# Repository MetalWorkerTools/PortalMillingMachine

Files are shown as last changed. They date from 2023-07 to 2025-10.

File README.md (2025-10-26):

# Portal Milling Machine
An easy to build portal milling machine for milling steel designed in FreeCad.
Most parts can be 3D printed to build the machine and milled out of aluminum when the machine is done to increase regidity.

Current progress: The machine is done except for a MQL system and some led illumination. I use the router for milling aluminum and steel and making PCB's. The result is pretty good but my manual mill is more rigid.
It would take about 100 hours to redo this machine from scratch. If you have a milling machine, you could directly make the aluminum version.

Backlash on all axis is somewhere between 0.01 and 0.03 mm.
I can adjust all axis to 0.02 mm / 100 mm.
The repeatability on all axis is better than 0.01 mm. (That is not the same as accuracy).
Without measuring, steel parts are within 0.1 mm. I haven't completed all tests but I expect that I can mill steel parts within 0.03 mm.
The self made 3000 RPM ER16 spindle is realy quit when milling. Because the frame is made from aluminium extrusion, the CNC router makes more noise than the manual mill under the same conditions.
The weight is about 55 kg.

For the next project I am going to CNC a manual mill that all ready has ball screws on the X and Y axis for more rigidity and lesser noise.

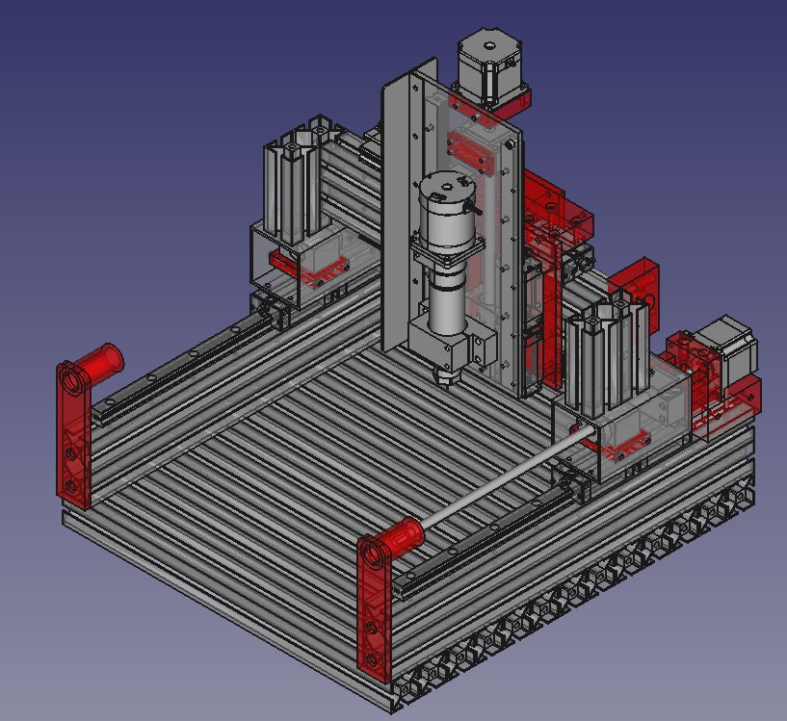
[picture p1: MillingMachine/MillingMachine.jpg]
MillingMachine


This page is under construction

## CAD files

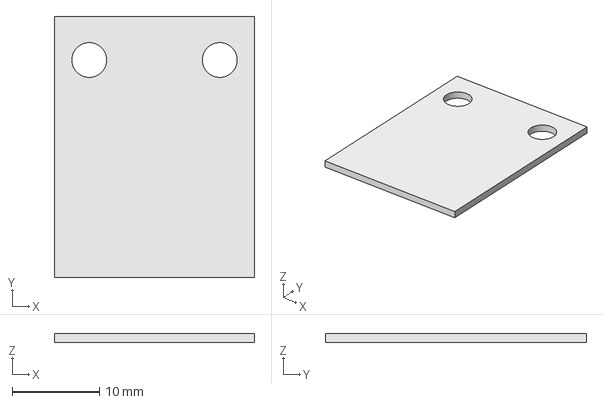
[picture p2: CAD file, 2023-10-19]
AirSuply/ValveMounting.FCStd
23.0 x 30.0 x 1.00 mm

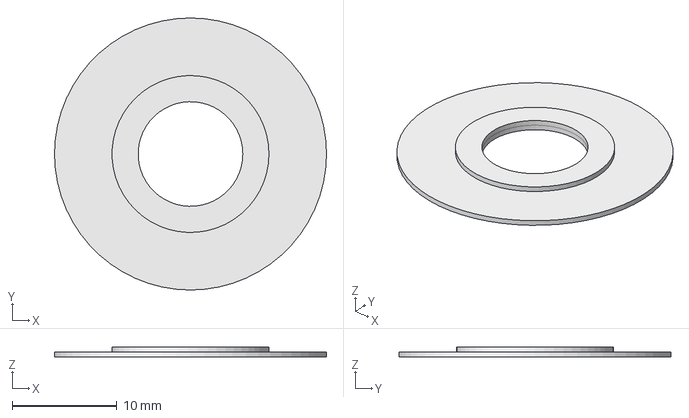
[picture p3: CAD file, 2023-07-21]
BK10BearingSpacer/BK10BearingSpacer.FCStd
26.0 x 26.0 x 1.00 mm

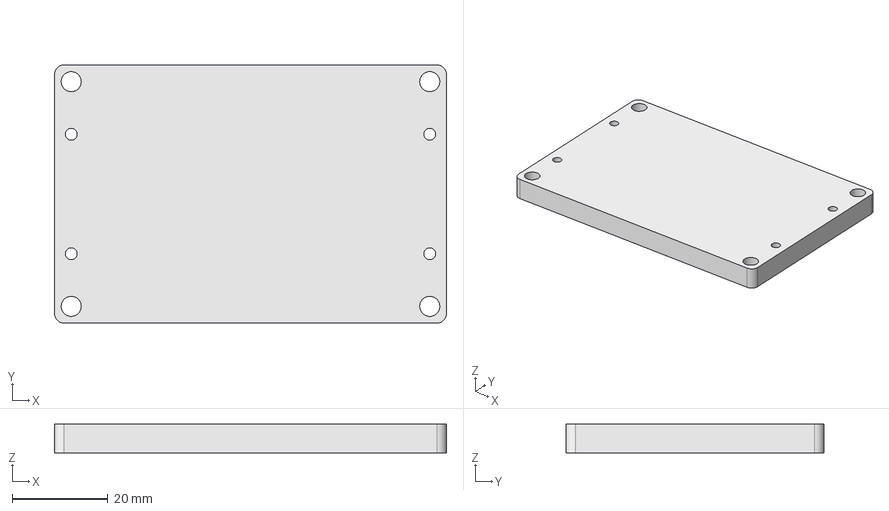
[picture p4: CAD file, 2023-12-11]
BLDC controller/BLDC controller.FCStd
82.0 x 54.0 x 6.00 mm

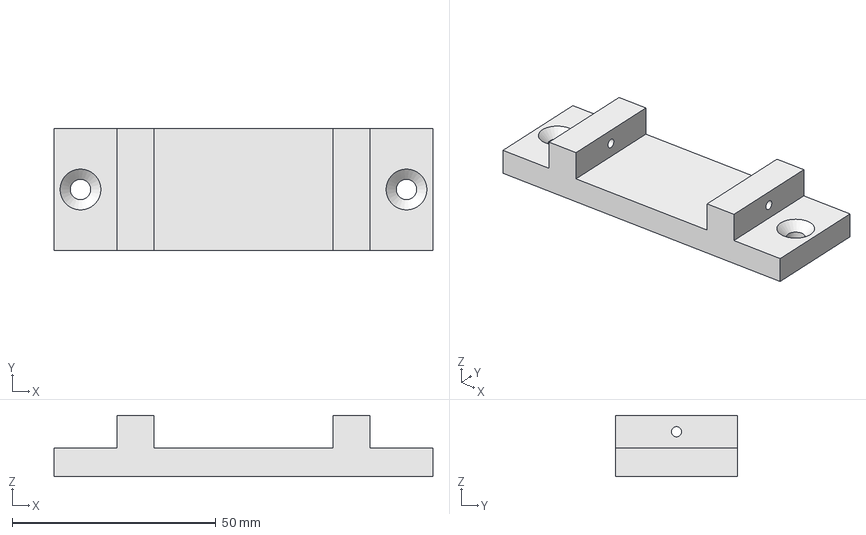
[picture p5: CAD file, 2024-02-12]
BridgeAngleAdjuster/BridgeAngleAdjuster.FCStd
93.0 x 30.0 x 15.0 mm

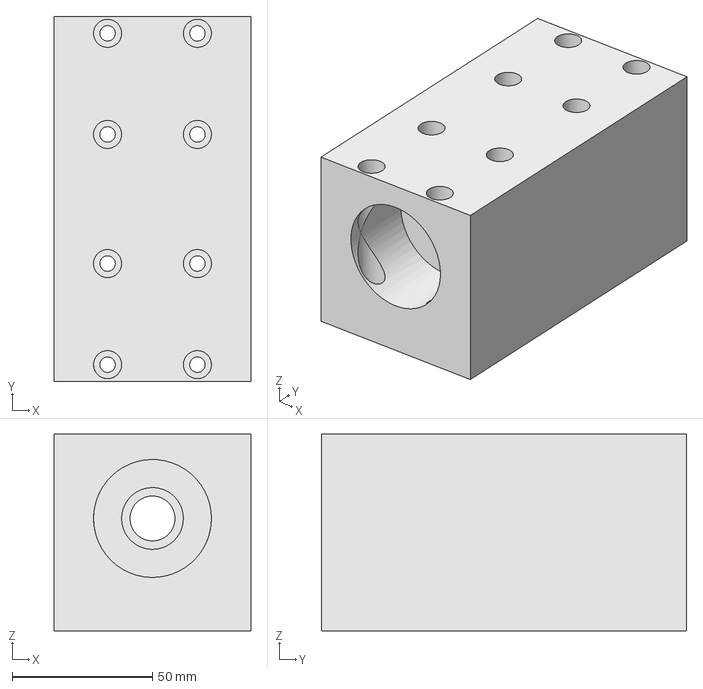
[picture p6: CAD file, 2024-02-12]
BridgeProfileSolid/BridgeProfileSolid.FCStd
70.0 x 130.0 x 70.0 mm

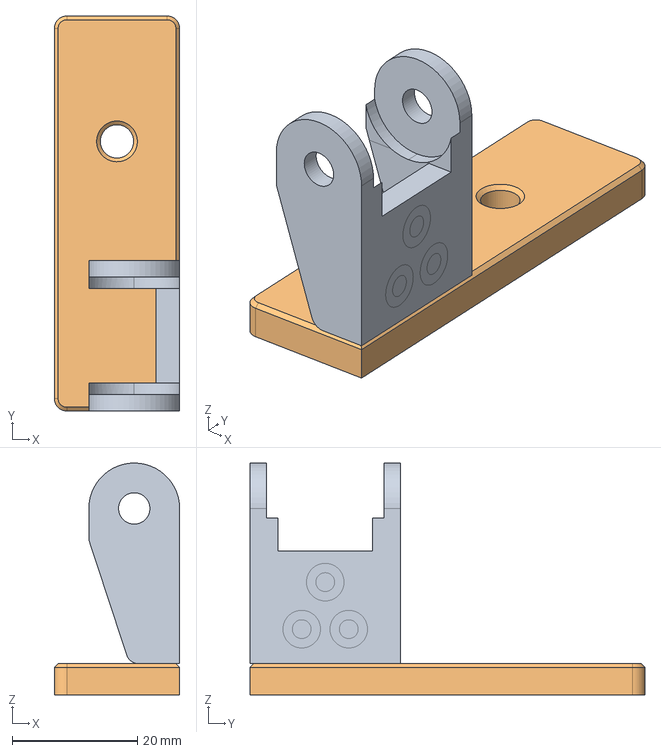
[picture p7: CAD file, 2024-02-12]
CableChain/CableChainMountXaxis.FCStd
20.0 x 63.0 x 37.0 mm
Chain
Base

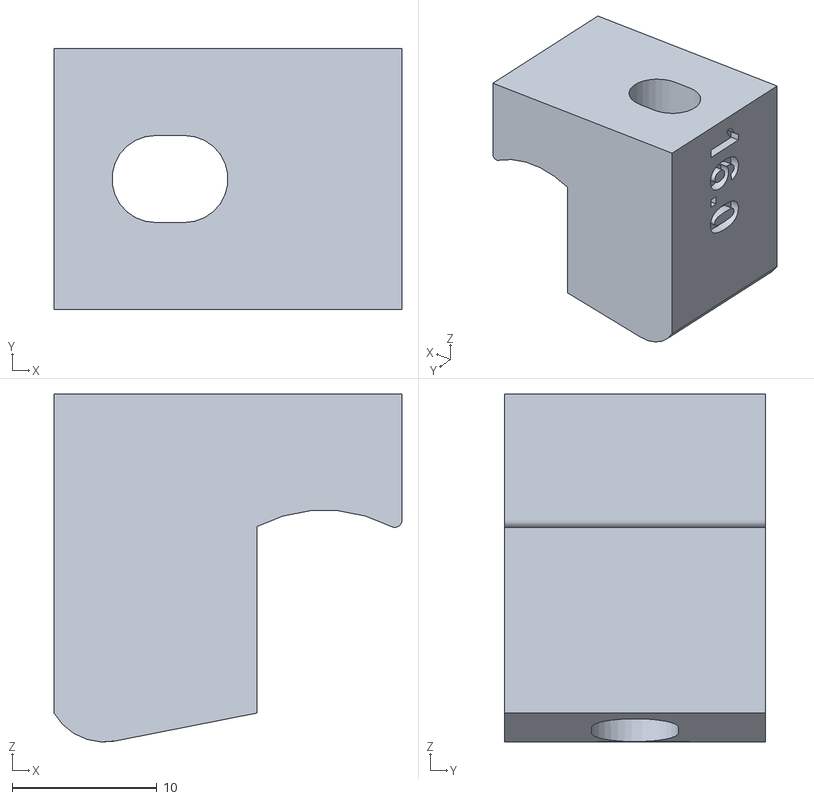
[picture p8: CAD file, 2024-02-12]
Clamps/ViceClamp.stl
24.0 x 18.0 x 24.0

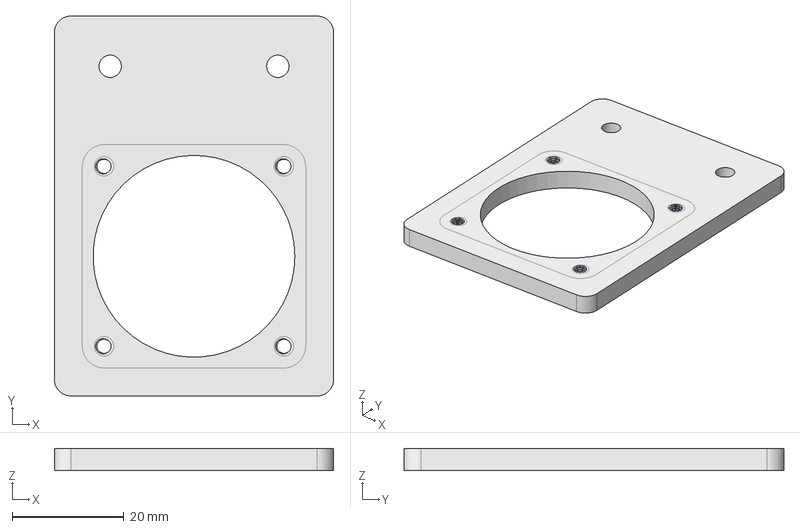
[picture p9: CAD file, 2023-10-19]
ControllerFanHolder/ControllerFanHolder.FCStd
50.0 x 68.0 x 4.00 mm

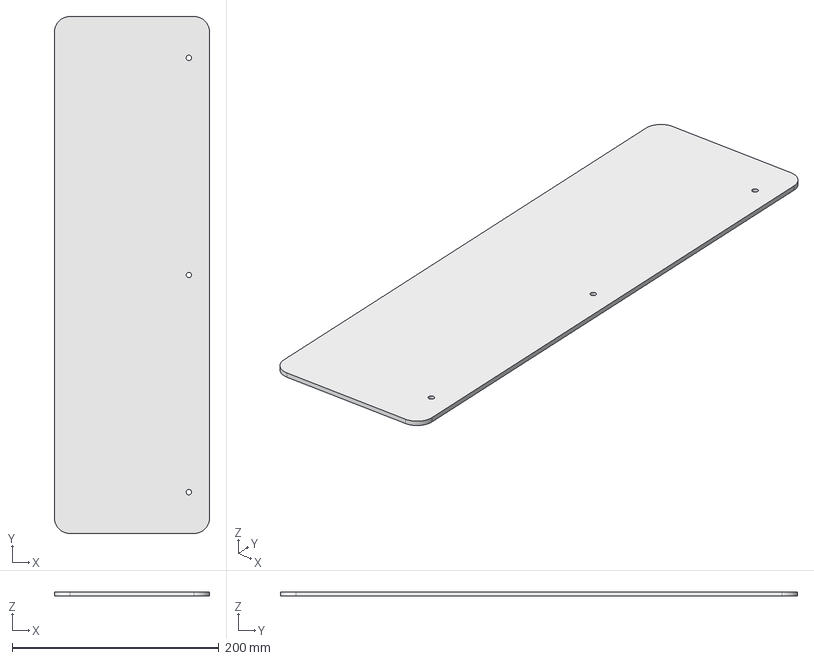
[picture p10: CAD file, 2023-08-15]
Covers/Covers.FCStd
150.0 x 500.0 x 4.00 mm

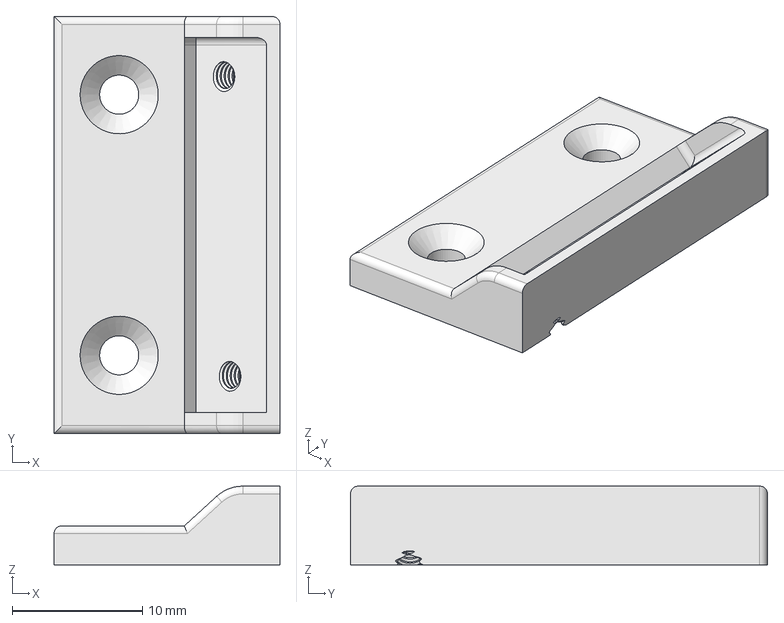
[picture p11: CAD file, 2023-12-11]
Display/DisplayHolder.FCStd
17.3 x 32.0 x 6.05 mm

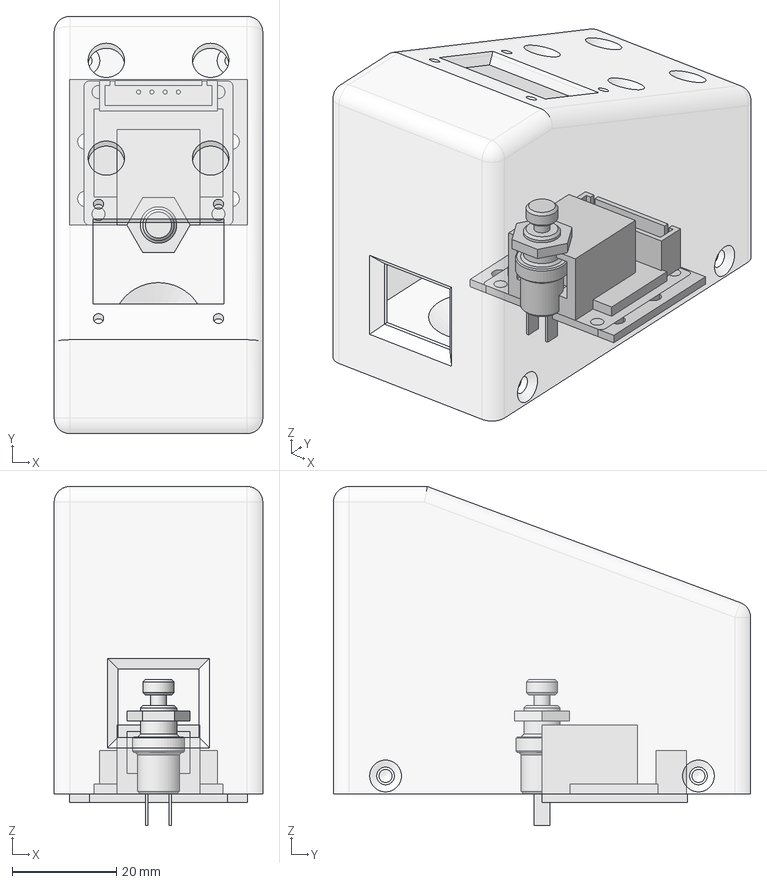
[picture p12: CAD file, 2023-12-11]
DisplayCase/DisplayCase.FCStd
40.0 x 80.0 x 65.0 mm
CaseBody
RJ45-JST-XH
Schakelaar
Display

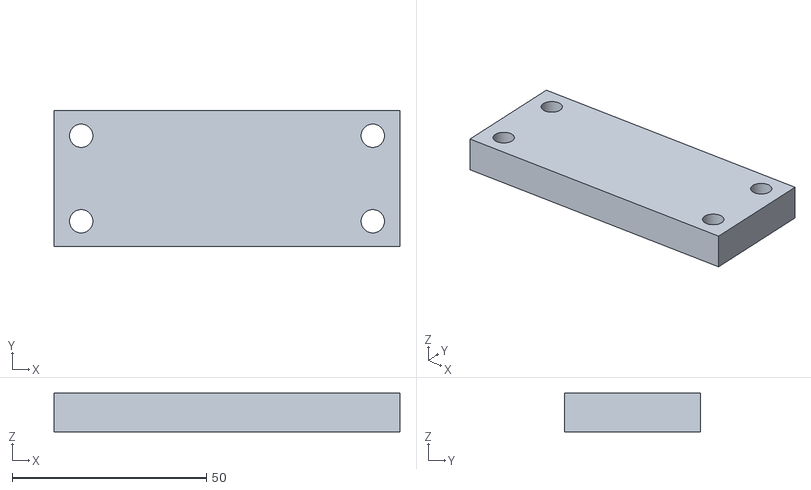
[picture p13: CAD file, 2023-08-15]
DremelSpindle/SpindleMountSpacer10mm.stl
89.0 x 35.0 x 10.0

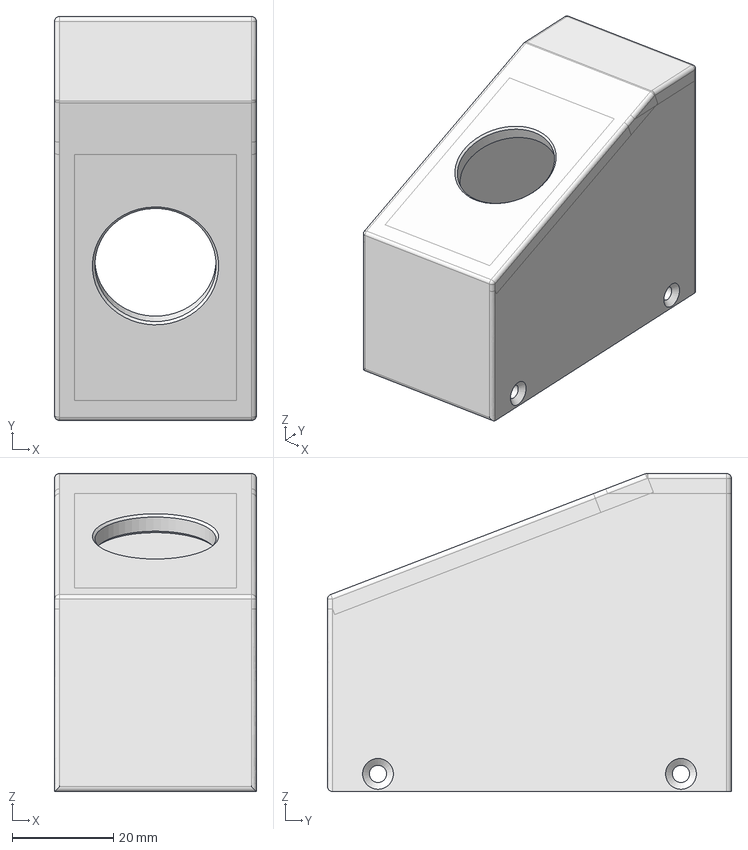
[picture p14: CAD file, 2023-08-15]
EmergencyButtonCase/EmergencyButtonCase.FCStd
40.0 x 80.0 x 63.0 mm

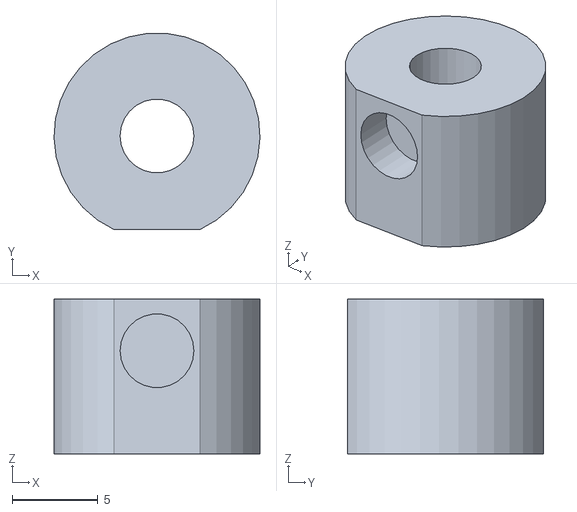
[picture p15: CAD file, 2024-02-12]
MillingMachine/MagnetHolder.stl
12.0 x 11.4 x 9.00

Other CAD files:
Probe/Probe.FCStd
RJ45 breakout board holder/RJ45 breakout board holder.FCStd
Spindle/ShaftCouplerBLDC57BFL03.stl
TransportHandles/TransportHandles.FCStd
AirSuply/AirHoseClamp.stl
AirSuply/AirTac 3V1 valve mounting.stl
AirSuply/AirValveAdapter.stl
AirSuply/AirValvePlug.stl
AirSuply/AirValvePlugG1_8.stl
BK10BearingSpacer/BK10BearingSpacer.stl
CableChain/CableChainEnd.FCStd
CableChain/CableChainMountXZaxis.FCStd
CableChain/CableChainMountXZaxisBase.stl
CableChain/CableChainMountXaxisBegin.stl
CableChain/CableChainMountYaxis.FCStd
CableChain/CableChainMountZaxis.FCStd
CableChain/CableChainMountZaxisBegin.stl
CableChain/CableChainMountZaxisEnd.stl
CableChain/YaxisCableChainMountingBegin.stl
CableChain/YaxisCableChainMountingEnd.stl
Clamps/AirHoseClamp.FCStd
Clamps/AirHoseClamp.stl
Clamps/BedClamp 10.stl
Clamps/BedClamp.stl
Clamps/BedClampShort 10.stl
Clamps/Clamps.FCStd
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

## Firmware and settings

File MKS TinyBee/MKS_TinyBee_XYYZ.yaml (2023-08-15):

# Run these commands at the serial terminal (fluidterm)
# press Ctrl U and upload the <FluidNC\example_configs\MKS_TinyBee_XYYZ.yaml> configuration file
# set the configuration filename by the next command
# $Config/Filename=MKS_TinyBee_XYYZ.yaml
# Reboot board
# run next commands to setup sta mode, ssid, password, hostname
# $WiFi/Mode=STA
# $Sta/SSID=YourWiFiRouterSSD
# $Sta/Password=YourWiFiRouterPassword
# $Hostname=YourMachineName
# Reboot board, in the serial terminal you will see the boot messages

#usefull commands:
# $Startup/Show     shows the startup messages
# $Limits           show the limit switch status realtime
# $NVX              erase settings. Do this to ensure only config file settings are used
# Current range X Y Z: 140 240 120

board: MKS TinyBee V1.0
name: Router XYYZ
meta: (28.07.2023) by MetalWorkerTools

kinematics:
  Cartesian:

stepping:
  engine: I2S_STATIC
  idle_ms: 0
  pulse_us: 4
  dir_delay_us: 1
  disable_delay_us: 0

axes:
  #default pin = high
  # X  
  x:
    steps_per_mm: 800
    max_rate_mm_per_min: 700.000
    acceleration_mm_per_sec2: 100.000
    max_travel_mm: 141.000
    soft_limits: true
    homing:
      cycle: 3
      positive_direction: false
      mpos_mm: 0.000
      feed_mm_per_min: 250.000
      seek_mm_per_min: 700.000
      settle_ms: 500
      seek_scaler: 1.100
      feed_scaler: 1.100
    #Motor X, CN=X
    motor0:
      limit_neg_pin: gpio.33:low:pd
      hard_limits: true
      pulloff_mm: 1.000
      stepstick:
        step_pin: I2SO.1
        direction_pin: I2SO.2:low
        disable_pin: I2SO.0

  y:
    # Y
    steps_per_mm: 800
    max_rate_mm_per_min: 700.000
    acceleration_mm_per_sec2: 100.000
    max_travel_mm: 241.000
    soft_limits: true
    homing:
      cycle: 2
      positive_direction: true
      mpos_mm: 0.000
      feed_mm_per_min: 250.000
      seek_mm_per_min: 700.000
      settle_ms: 500
      seek_scaler: 1.100
      feed_scaler: 1.100
     #Motor Y1, CN=Y
    motor0:
      limit_neg_pin: gpio.32:low:pu
      hard_limits: true
      pulloff_mm: 1.000
      stepstick:
        step_pin: I2SO.4
        direction_pin: I2SO.5
        disable_pin: I2SO.3
    #Motor Y2, CN=E1
    motor1:
      limit_neg_pin: gpio.35:low:pu
      # hard_limits: true
      pulloff_mm: 1.000
      stepstick:
        step_pin: I2SO.10
        direction_pin: I2SO.11
        disable_pin: I2SO.9

  z:
    # Z
    steps_per_mm: 800
    max_rate_mm_per_min: 700.000
    acceleration_mm_per_sec2: 150.000
    max_travel_mm: 120.000
    soft_limits: true
    homing:
      cycle: 1
      positive_direction: true
      mpos_mm: 0.000
      feed_mm_per_min: 250.000
      seek_mm_per_min: 700.000
      settle_ms: 500
      seek_scaler: 1.100
      feed_scaler: 1.100
    #Motor Z, CN=Z
    motor0:
      limit_pos_pin: gpio.22:low:pu
      hard_limits: true
      pulloff_mm: 1.000
      stepstick:
        step_pin: I2SO.7
        direction_pin: I2SO.8:low
        disable_pin: I2SO.6

i2so:
  bck_pin: gpio.25
  data_pin: gpio.27
  ws_pin: gpio.26

spi:
  miso_pin: gpio.19
  mosi_pin: gpio.23
  sck_pin: gpio.18

# sdcard:
#   cs_pin: gpio.5
#   card_detect_pin: NO_PIN

control:
  estop_pin: gpio.36
  safety_door_pin: NO_PIN
  reset_pin: NO_PIN
  feed_hold_pin: NO_PIN
  cycle_start_pin: NO_PIN
  # EXP1 BTN_ENC
  # macro0_pin: gpio.4:low:pu
  macro0_pin: NO_PIN
  macro1_pin: NO_PIN
  macro2_pin: NO_PIN
  macro3_pin: NO_PIN


macros:
  startup_line0:
  startup_line1:
  macro0: $LocalFs/Run=Macro0.gcode
  macro1: 
  macro2:
  macro3:

coolant:
  flood_pin: NO_PIN
  mist_pin: NO_PIN
  delay_ms: 0

probe:
  # TB input
  # tested OK
  pin: gpio.39:low
  # Warning: 3Dtouch connector Pinout differs from limit switches 1=signal 2=5V 3+GND, gpio.2 doesn't work as input 
  toolsetter_pin: NO_PIN
  

  check_mode_start: true

user_outputs:
  analog0_pin: NO_PIN
  analog1_pin: NO_PIN
  analog2_pin: NO_PIN
  analog3_pin: NO_PIN
  analog0_hz: 5000
  analog1_hz: 5000
  analog2_hz: 5000
  analog3_hz: 5000
  digital0_pin: NO_PIN
  digital1_pin: NO_PIN
  digital2_pin: NO_PIN
  digital3_pin: NO_PIN

start:
  must_home: false
# # Spindle disabled because it is not connected at the moment  
# # spindle PWM signal
# PWM:
#   pwm_hz: 2500
#   # on EXP1 IO15 connector.
#   # note IO15 will give some short pulses on boot, which may activate spindle
#   # use IO17 on EXP1 to avoid
#   output_pin: gpio.15:high
#   s0_with_disable: true
#   tool_num: 0
#   spinup_ms: 4000
#   spindown_ms: 4000
#   speed_map: 0=0.000% 12000=100.000%

# Oled disabled because it is not connected at the moment
# i2c0:
#    sda_pin: gpio.14
#    scl_pin: gpio.13

# oled:
#    i2c_num: 0
#    i2c_address: 60
#    width: 128
#    height: 64
#    radio_delay_ms: 1000

# oled I2 connection:
# Warning, connector housing on the tinybee board is wrong, rotated 180°. Pin 1 mark (square solder pad) is OK.
# Tested using 128x64 SDD1306 LCD
# EXP1-2 = SCL
# EXP2-3 = SDA
# EXP2-9 = VCC (3v3)
# EXP2-10 = GND

 # USB  TX0(1)  RX0(3)
 # J3-> TX2(17) RX2(16)
 # J1-> I2SO.23 I2SO.22
 # TH1(36)        TH2(34)        THB(39)
 # HE0(I2SO.17)   HE1(I2SO.18)   HBED(I2SO.16)
 # FAN1(I2SO.19)  FAN2(I2SO.20)
 #                   EXP1                                   EXP2
 #(BEEPER) I2SO.21 | 1  2 | 13 (BTN_ENC)    (SPI MISO) 19 | 1  2 | 18 (SPI SCK)
 #    (LCD_EN)  21 | 3  4 |  4 (LCD_RS)      (BTN_EN1) 14 | 3  4 |  5 (SPI CS)
 #    (LCD_D4)   0 | 5  6   16 (LCD_D5)      (BTN_EN2) 12 | 5  6   23 (SPI MOSI)
 #    (LCD_D6)  15 | 7  8 | 17 (LCD_D7)      (SPI_DET) 34 | 7  8 | RESET
 #             GND | 9 10 | 5V                        GND | 9 10 | 3.3V

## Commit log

2023-07-02 Build the bed
    [MillingSpindleER16.FCStd]
2023-07-06 Design adjusted
    Several changes and fixes
    [RailAdjuster.stl, YaxisBK10Spacer.stl]
2023-07-10 Build and tested Y-axis
    Yaxis build and tested
    Updated Y-axis
    Yaxis BK10 spacer done
    Added YaxisBK10Spacer
    Start making Yaxis BK10 spacer
    Changed Yaxis Stepper holder. Sketcher OK
    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
    [YaxisBK10Spacer.stl]
2023-07-15 Build and tested X-axis
2023-07-21 Build the Z-axis
    Added support angle bracket to Zaxis plate
    [BK10BearingSpacer.FCStd]
2023-08-15 Added a probe sensor, Estop and MKS TinyBee Configuration
    [BedClamp23mm.stl, BedClamp4mm.stl, BedClamp8mm.stl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]
2023-10-19 Finalized design milling spindle
    [AirHoseClamp.stl, AirTac 3V1 valve mounting.stl, AirValveAdapter.stl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]
2023-10-19 Added design for the (full) aluminum version
    I am replacing some 3D printed parts for aluminum parts. This allows some minor changes to reduce the number of parts.
    The MillingMachineAluminum.FCStd file contains the design for the aluminum version.
2023-12-11 Milled all aluminum parts and moved the X-axis home sensor
    [AirHoseClamp.FCStd, AirHoseClamp.stl, BLDC controller.FCStd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]
2024-02-12 Changed carriage profile and y-axis ball nut housing to improve rigidity
    Added a probe cap as dust protection
    Added a probe cap
    Update MillingMachineAluminum.FCStd
    Added path jobs for milling bridge carriage profile
    Update MillingMachineAluminum.FCStd
    Changed Y-axis carriage profile to 2 hole mount
    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
    [BridgeAngleAdjuster.FCStd, BridgeHeightAdjuster.stl, BridgeProfileSolid.FCStd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]
2025-10-26 Revise current progress.
    Updated current progress and spindle description in README.
